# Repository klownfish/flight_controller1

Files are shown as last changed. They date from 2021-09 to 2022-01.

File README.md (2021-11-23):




The goal for the flight controller is to

1. Measure acceleration, rotation and altitude
1. Get rocket location
1. Store all measurements on-board
1. Real-time telemetry
1. Ignite explosive charges
1. Record video

So far it has been used on [rocket1](https://github.com/klownfish/rocket1) and my W.I.P guided rocket.

### Sensors

The altitude is calculated from the pressure using a BMP280 pressure sensor. The accuracy is about +-1m which is good enough for determining the apogee but acceleration and velocity is pretty much completely lost in the noise. Acceleration and rotation is gathered from a MPU9250 which sucks hard unfortunately. The gyroscope drifts rapidly and so there is no way to get the an accurate attitude estimate. Both of these sensors are available on a GY-91 breakout board.

A Ublox M8 GPS from Team Blacksheep measured the location. The Ublox chip is easy to configure and use but the module I chose does not have any moutning holes…

### Telemetry
All data is stored on a Winond NOR flash IC and it does what it’s supposed to do. I wanted to use a RF96 LoRa modem but I mixed up the numbers ordered a RF69 generic GFSK modem. It works alright so it didn’t really matter in the end. I have not conducted a real range test but the “GFSK_Rb38_4Fd76_8” profile worked for my 30m launches.

### Pyro channels
The pyro channels consist of half H-bridges connected to GND and 12V. A half bridge is necessary to keep the channel shorted when not in use. A TVS diode is connected in parallel as well to protect from electrostatic discarges. BTN7030-1EPA is an awesome “smart” half bridge IC and powers all the channels. It has built in short circuit and overheat protection. It can source 14 Amps of currents which is on the low side for what I want to do. Running of a 3s LiPo battery at 12.6v it can power a 1.1 Ohm load which is very close to the resistance of an ignitor. From empirical data it has worked four out four times so far.

As an additional safety measure a jumper can overwrite the logic output from the micro controller and force all enable pins low. Two LEDs also show if the channels are armed or not.

### Video
A runcam split 4 recorded the onboard footage and I can not recommend it. The auto record function just straight up does not work so it doesn’t record on start up. As a result you have to push a button to start the recording manually and good luck doing that when it’s mounted inside a nose cone. Good thing the camera only cost 80€ and was destroyed in a crash. I hate that camera so fucking much I am so mad AAAAAAHHH

### Guidance
This flight controller is currently the base for a guided rocket that i am developing. It's possible to connect a BMI088 IMU to the expansion port which is much more accurate than the MPU9250. The UART pins for the GPS can also be used to control 2 servos. The servos are connected to a pyro channel with an external voltage regulator.

### Dashboard
The dashboard is written in python using TK and Matplotlib.

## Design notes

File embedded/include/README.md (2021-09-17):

If you are an radio amateur please create a file named `callsign.h` that contains your callsign.

It should look like this `#define CALLSIGN "xxxxxx"`

The code will adjust the TX properties depending on if you have a license or not. 

It might be illegal to run this without an license even though the TX power is lowered since the duty cycle can go over 10%.

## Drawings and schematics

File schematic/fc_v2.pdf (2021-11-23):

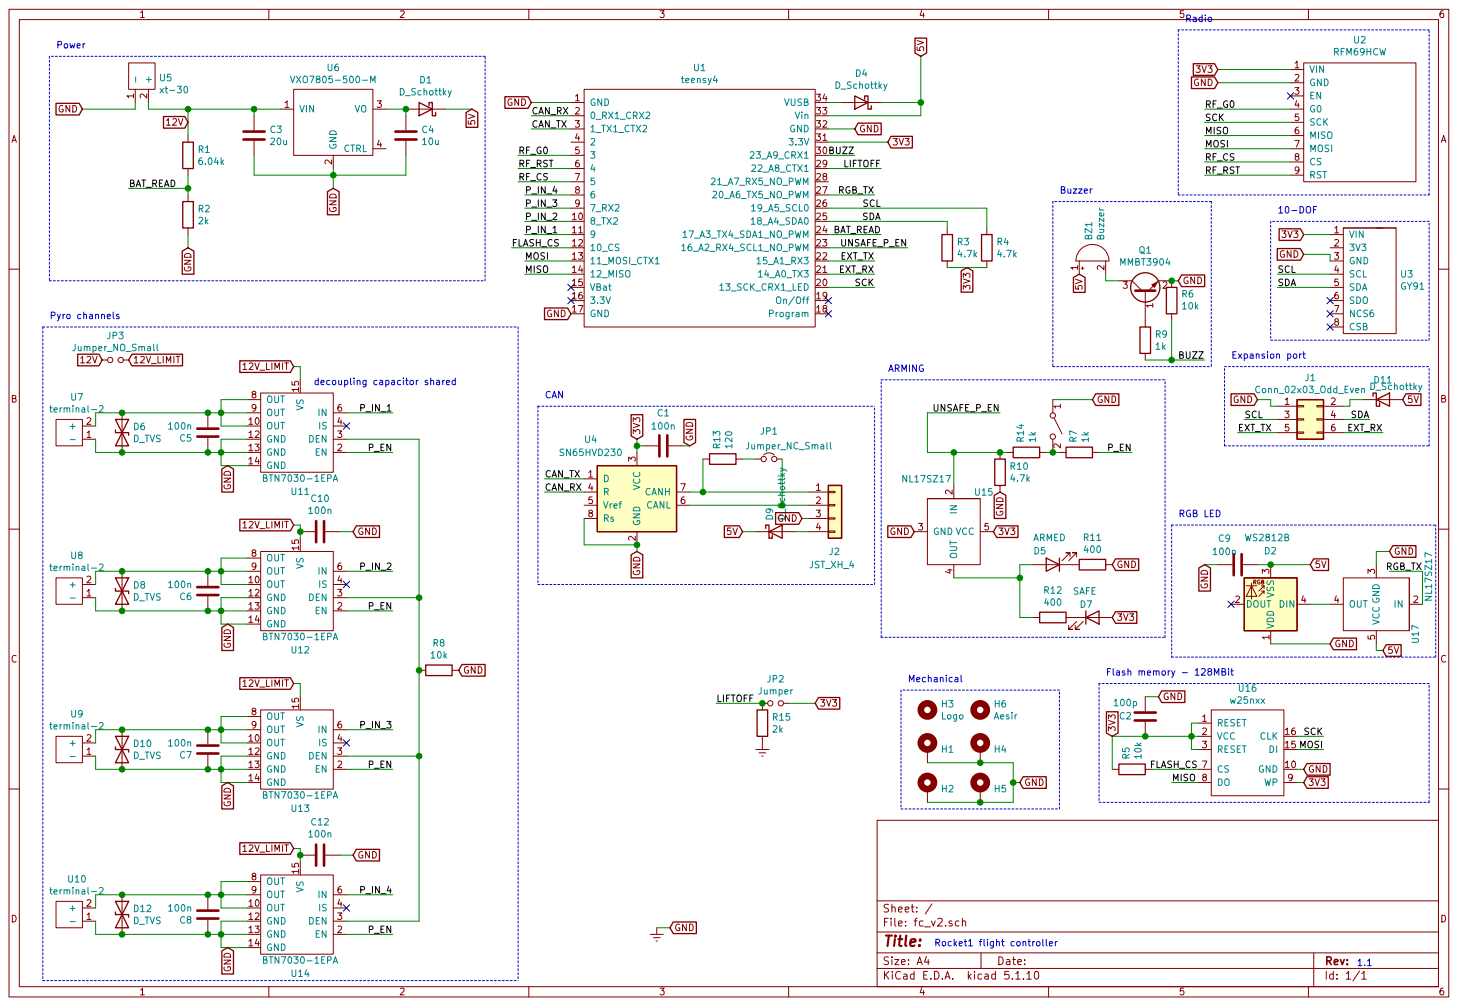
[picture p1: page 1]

Expansion port Buzzer CAN

Flash memory - 128MBit RGB LED

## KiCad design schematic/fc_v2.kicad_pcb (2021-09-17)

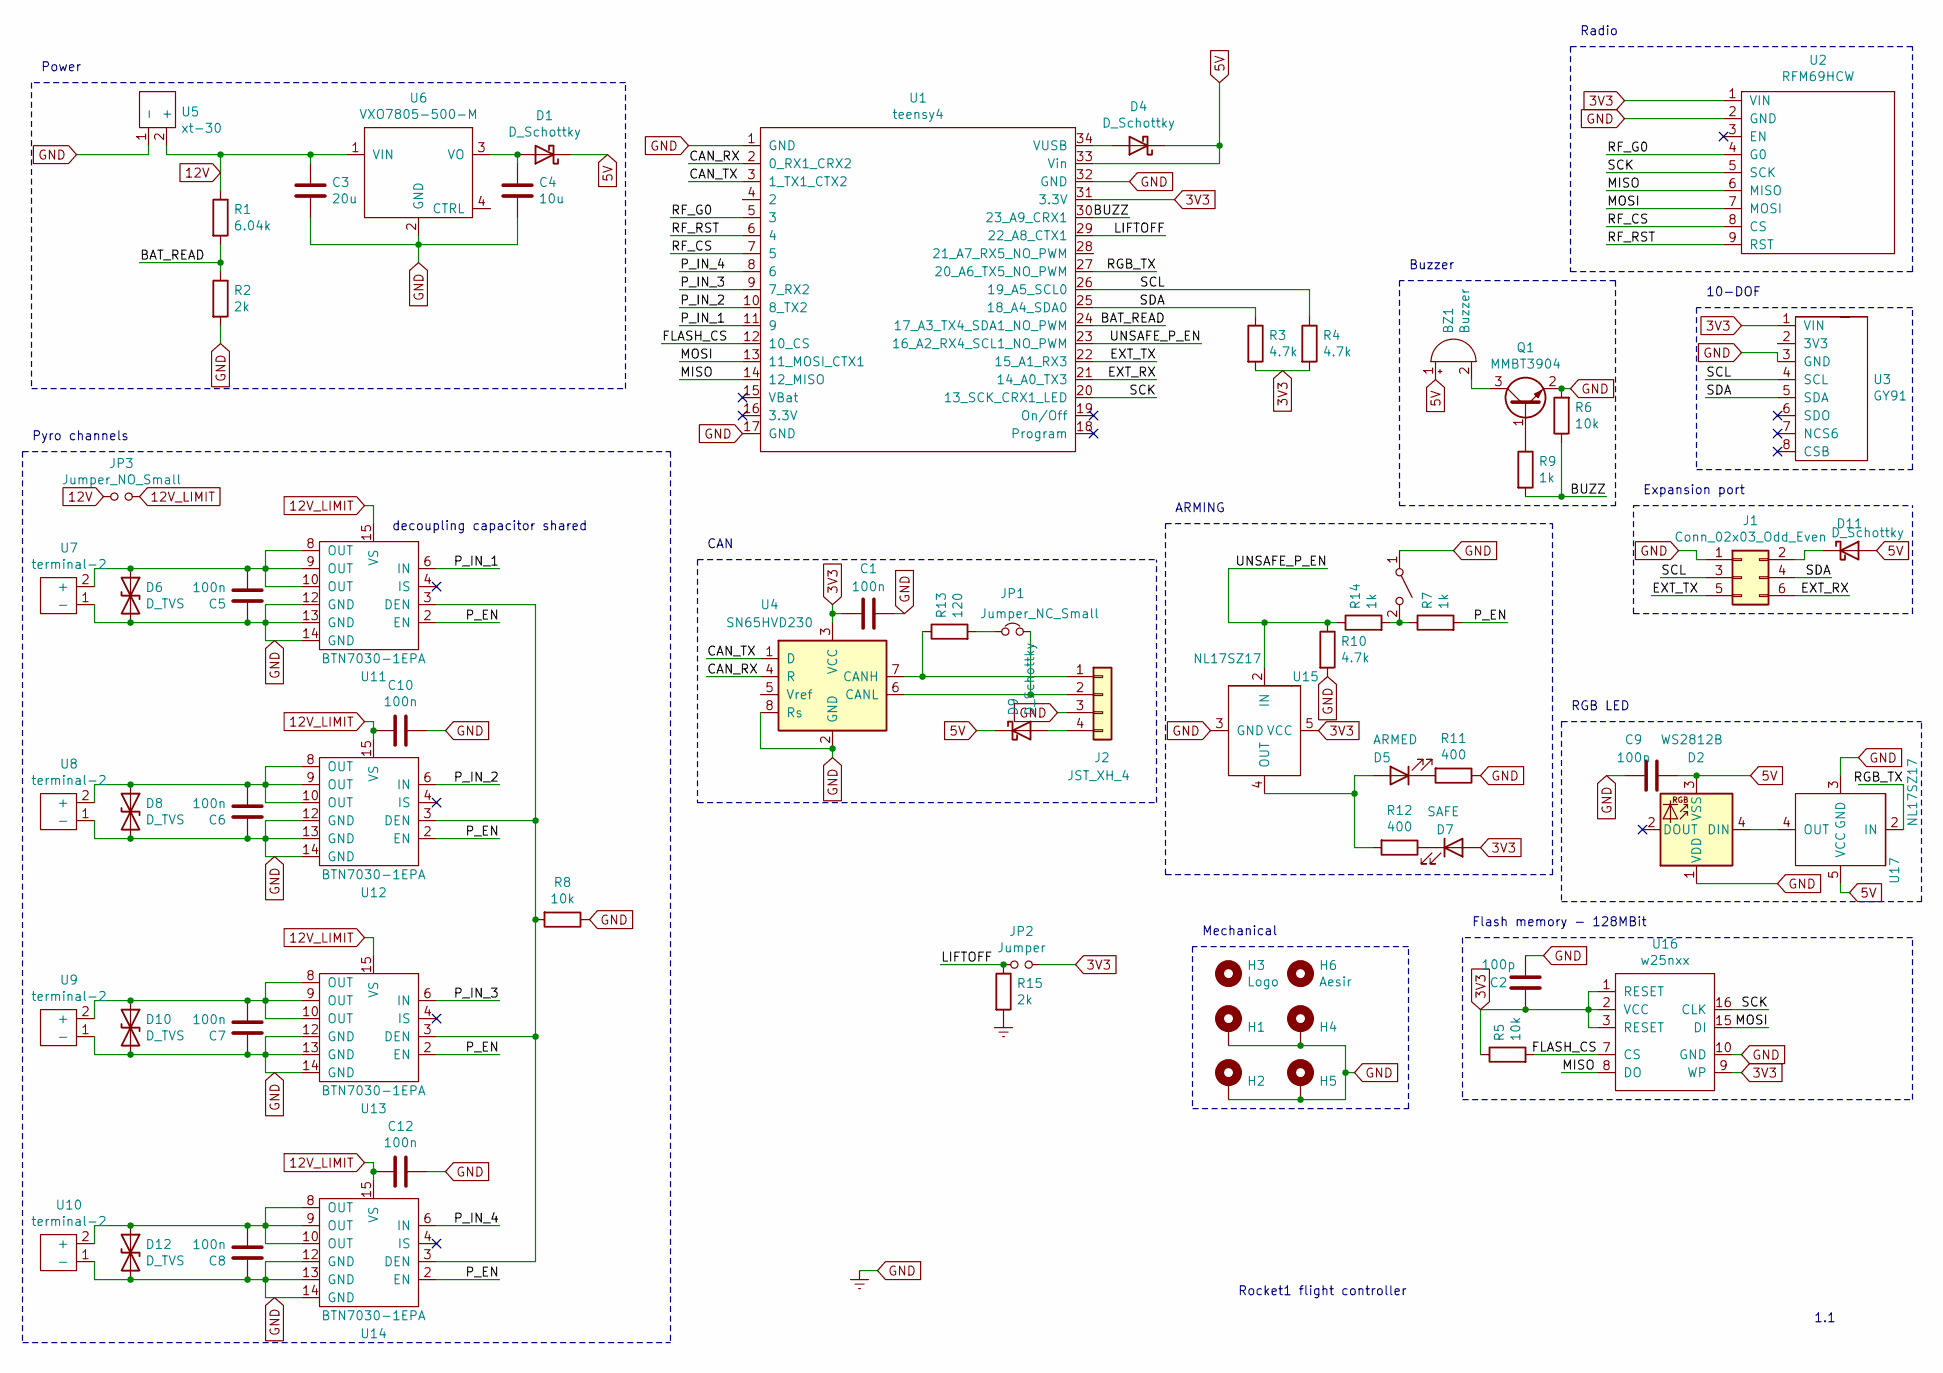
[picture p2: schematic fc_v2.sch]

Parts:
BZ1: Buzzer; CX-0905C
C1, C5, C6, C7, C8, C9, C10, C12: 100n; C_0805_2012Metric_Pad1.18x1.45mm_HandSolder
C2: 100p; C_0805_2012Metric_Pad1.18x1.45mm_HandSolder
C3: 20u; C_0805_2012Metric_Pad1.18x1.45mm_HandSolder
C4: 10u; C_0805_2012Metric_Pad1.18x1.45mm_HandSolder
D1, D4, D9, D11: D_Schottky; D_SOD-323_HandSoldering
D2: WS2812B; ws2812-through-hole-5mm
D5: ARMED; LED_0805_2012Metric_Pad1.15x1.40mm_HandSolder
D6, D8, D10, D12: D_TVS; D_0805_2012Metric_Pad1.15x1.40mm_HandSolder
D7: SAFE; LED_0805_2012Metric_Pad1.15x1.40mm_HandSolder
H1, H2, H4, H5: MountingHole_Pad; MountingHole_2.2mm_M2_Pad_Via
H3: Logo; avatar
H6: Aesir; aesir
J1: Conn_02x03_Odd_Even; PinHeader_2x03_P2.54mm_Vertical
J2: JST_XH_4; JST_XH_B4B-XH-A_1x04_P2.50mm_Vertical
JP1: Jumper_NC_Small; PinHeader_1x02_P2.54mm_Vertical
JP2: Jumper; JST_XH_B2B-XH-A_1x02_P2.50mm_Vertical
JP3: Jumper_NO_Small; R_1812_4532Metric_Pad1.30x3.40mm_HandSolder_no_silk
Q1: MMBT3904; SOT-23
R1: 6.04k; R_0805_2012Metric_Pad1.20x1.40mm_HandSolder
R2, R15: 2k; R_0805_2012Metric_Pad1.20x1.40mm_HandSolder
R3, R4, R10: 4.7k; R_0805_2012Metric_Pad1.20x1.40mm_HandSolder
R5, R6, R8: 10k; R_0805_2012Metric_Pad1.20x1.40mm_HandSolder
R7, R9, R14: 1k; R_0805_2012Metric_Pad1.20x1.40mm_HandSolder
R11, R12: 400; R_0805_2012Metric_Pad1.20x1.40mm_HandSolder
R13: 120; R_0805_2012Metric_Pad1.20x1.40mm_HandSolder
SW1: SW_DPST_x2; PinHeader_1x02_P2.54mm_Vertical
U1: teensy4
U2: RFM69HCW; Adafruit-RFM69
U3: GY91
U4: SN65HVD230; SOIC-8_3.9x4.9mm_P1.27mm
U5: xt-30; AMASS_XT30U-M_1x02_P5.0mm_Vertical
U6: VXO7805-500-M
U7, U8, U9, U10: terminal-2; terminal-small
U11, U12, U13, U14: BTN7030-1EPA; Infineon_PG-TSDSO-14-22-bottom
U15, U17: NL17SZ17; SC-74-a
U16: w25nxx; SOIC-16W_7.5x10.3mm_P1.27mm

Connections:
3V3: C1.2, C2.1, D7.2 (A), JP2.2, R3.2, R4.2, R5.1, U1.31 (3.3V), U2.1 (VIN), U3.1 (VIN), U4.3 (VCC), U15.5 (VCC), U16.1 (RESET), U16.2 (VCC), U16.3 (RESET), U16.9 (WP)
5V: BZ1.1 (-), C9.1, D1.1 (K), D2.3 (VSS), D4.1 (K), D9.1 (K), D11.2 (A), U1.33 (Vin), U17.5 (VCC)
12V: C3.1, JP3.1, R1.1, U5.2 (+), U6.1 (VIN)
12V_LIMIT: C10.2, C12.2, JP3.2, U11.15 (VS), U12.15 (VS), U13.15 (VS), U14.15 (VS)
/BAT_READ: R1.2, R2.1, U1.24 (17_A3_TX4_SDA1_NO_PWM)
/BUZZ: R6.1, R9.2, U1.30 (23_A9_CRX1)
/CAN_RX: U1.2 (0_RX1_CRX2), U4.4 (R)
/CAN_TX: U1.3 (1_TX1_CTX2), U4.1 (D)
/EXT_RX: J1.6, U1.21 (14_A0_TX3)
/EXT_TX: J1.5, U1.22 (15_A1_RX3)
/FLASH_CS: R5.2, U1.12 (10_CS), U16.7 (CS)
/LIFTOFF: JP2.1, R15.1, U1.29 (22_A8_CTX1)
/MISO: U1.14 (12_MISO), U2.6 (MISO), U16.8 (DO)
/MOSI: U1.13 (11_MOSI_CTX1), U2.7 (MOSI), U16.15 (DI)
/P_EN: R7.2, U11.2 (EN), U12.2 (EN), U13.2 (EN), U14.2 (EN)
/P_IN_1: U1.11 (9), U11.6 (IN)
/P_IN_2: U1.10 (8_TX2), U12.6 (IN)
/P_IN_3: U1.9 (7_RX2), U13.6 (IN)
/P_IN_4: U1.8 (6), U14.6 (IN)
/RF_CS: U1.7 (5), U2.8 (CS)
/RF_G0: U1.5 (3), U2.4 (G0)
/RF_RST: U1.6 (4), U2.9 (RST)
/RGB_TX: U1.27 (20_A6_TX5_NO_PWM), U17.2 (IN)
/SCK: U1.20 (13_SCK_CRX1_LED), U2.5 (SCK), U16.16 (CLK)
/SCL: J1.3, R4.1, U1.26 (19_A5_SCL0), U3.4 (SCL)
/SDA: J1.4, R3.1, U1.25 (18_A4_SDA0), U3.5 (SDA)
/UNSAFE_P_EN: R10.1, R14.1, U1.23 (16_A2_RX4_SCL1_NO_PWM), U15.2 (IN)
GND: C1.1, C2.2, C3.2, C4.2, C5.1, C6.1, C7.1, C8.1, C9.2, C10.1, C12.1, D2.1 (VDD), D6.2 (A2), D8.2 (A2), D10.2 (A2), D12.2 (A2), H1.1, H2.1, H4.1, H5.1, J1.1, J2.3, Q1.2 (E), R2.2, R6.2, R8.1, R10.2, R11.1, R15.2, SW1.1 (A), U1.1 (GND), U1.17 (GND), U1.32 (GND), U2.2 (GND), U3.3 (GND), U4.2 (GND), U4.8 (Rs), U5.1 (-), U6.2 (GND), U7.1 (-), U8.1 (-), U9.1 (-), U10.1 (-), U11.12 (GND), U11.13 (GND), U11.14 (GND), U12.12 (GND), U12.13 (GND), U12.14 (GND), U13.12 (GND), U13.13 (GND), U13.14 (GND), U14.12 (GND), U14.13 (GND), U14.14 (GND), U15.3 (GND), U16.10 (GND), U17.3 (GND)
unnamed: BZ1.2 (+), Q1.3 (C)
unnamed: C4.1, D1.2 (A), U6.3 (VO)
unnamed: C5.2, D6.1 (A1), U7.2 (+), U11.8 (OUT), U11.9 (OUT), U11.10 (OUT)
unnamed: C6.2, D8.1 (A1), U8.2 (+), U12.8 (OUT), U12.9 (OUT), U12.10 (OUT)
unnamed: C7.2, D10.1 (A1), U9.2 (+), U13.8 (OUT), U13.9 (OUT), U13.10 (OUT)
unnamed: C8.2, D12.1 (A1), U10.2 (+), U14.8 (OUT), U14.9 (OUT), U14.10 (OUT)
unnamed: D2.4 (DIN), U17.4 (OUT)
unnamed: D4.2 (A), U1.34 (VUSB)
unnamed: D5.1 (K), R11.2
unnamed: D5.2 (A), R12.2, U15.4 (OUT)
unnamed: D7.1 (K), R12.1
unnamed: D9.2 (A), J2.4
unnamed: D11.1 (K), J1.2
unnamed: J2.1, R13.1, U4.7 (CANH)
unnamed: J2.2, JP1.2, U4.6 (CANL)
unnamed: JP1.1, R13.2
unnamed: Q1.1 (B), R9.1
unnamed: R8.2, U11.3 (DEN), U12.3 (DEN), U13.3 (DEN), U14.3 (DEN)
unnamed: R7.1, R14.2, SW1.2 (B)

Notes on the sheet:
Rocket1 flight controller
1.1
Flash memory - 128MBit
Radio
Power
RGB LED
Expansion port
Buzzer
ARMING
Pyro channels
decoupling capacitor shared
Mechanical
10-DOF
CAN

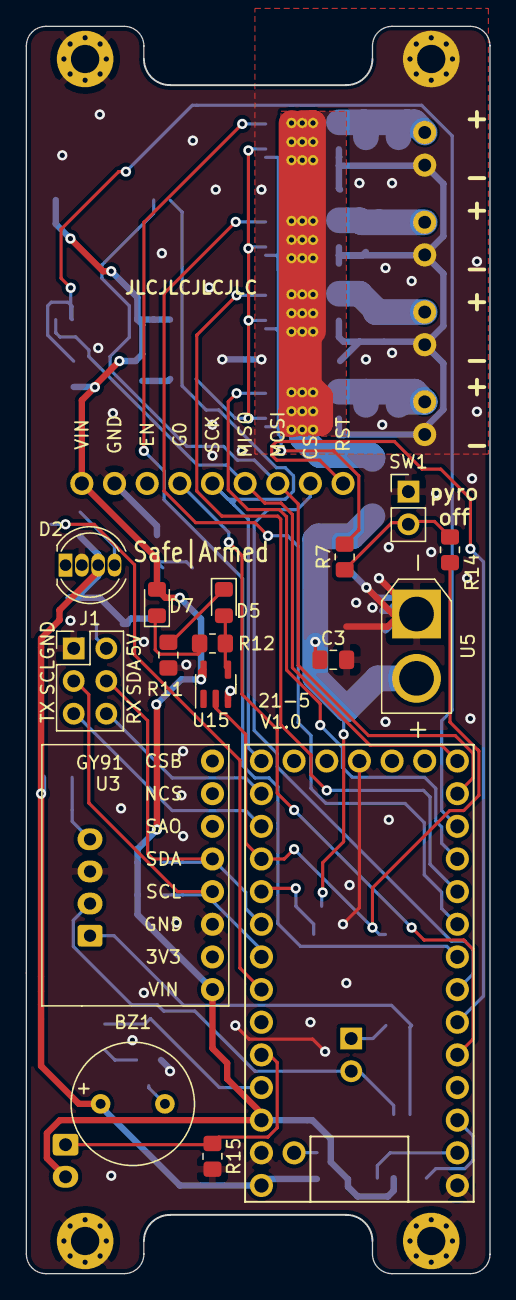
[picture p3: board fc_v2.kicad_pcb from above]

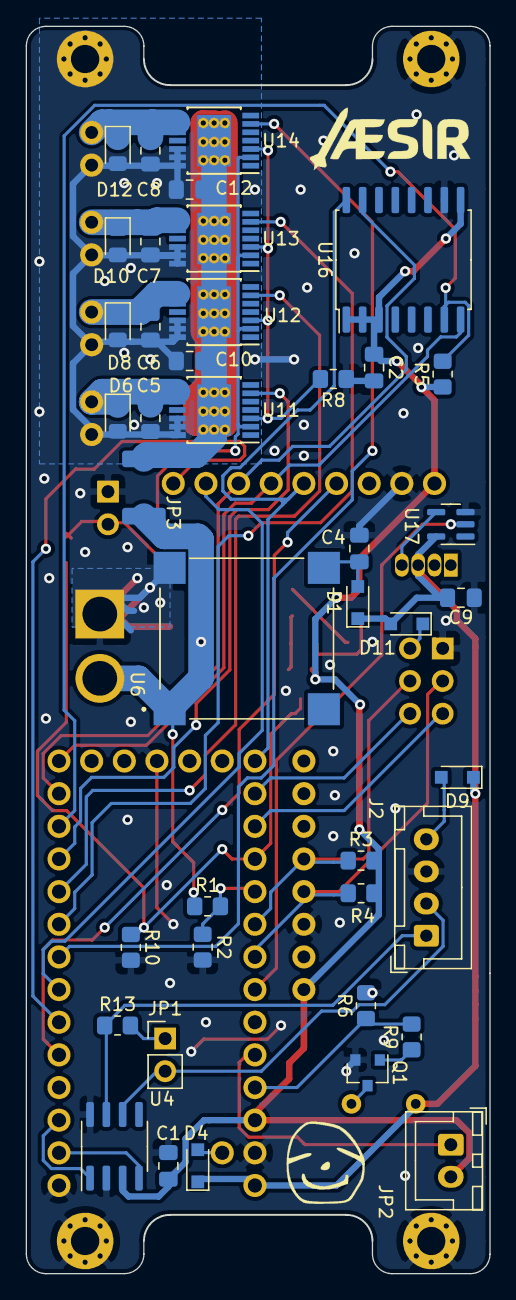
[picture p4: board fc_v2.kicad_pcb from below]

Board: 2 copper layers, 36.1 x 97.0 mm, 68 parts (47 on the bottom side), 47 nets.

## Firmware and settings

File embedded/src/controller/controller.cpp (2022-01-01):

#include <Arduino.h>
#include <SPI.h>
#include <RH_RF69.h>
#include <Adafruit_BMP280.h>
#include <elapsedMillis.h>
#include <WS2812Serial.h>
#include <Adafruit_NeoPixel.h>

#include "definitions.h" // pin and protocol definitions
#include "controller.h"
#include "rocket.h"
#include "protocol.h"
#include "Sampler.h"

//haha lolz
void dance();

#define SERIAL_DEBUG

#define TIME_HZ 1000
#define BMI_GYRO_HZ 1000
#define BMI_ACCEL_HZ 250
#define BMP_HZ 50
#define BATTERY_HZ 10
#define BATTERY_HZ 10
#define GPS_HZ 10
#define TELEMETRY_HZ 15
#define STATE_HZ 100
#define TVC_ANGLE_HZ 400

#define FLASH_TEST_BYTES 10

#define GPS_BAUD 9600

#define SERVO_MIN_PULSE 750
#define SERVO_MAX_PULSE 2250
#define SERVO_ACTUATION (55 * DEG_TO_RAD)

//#define USE_GPS
#define USE_SERVO

#ifdef USE_GPS
#ifdef USE_SERVO
#error "Both servo and gps in use"
#endif
#endif

#define KP 0.5 
#define KI 0.05
#define KD 0.2

Threads::Mutex i2c_mtx;
Threads::Mutex spi_mtx;
Threads::Mutex usb_mtx;

byte drawingMemory[3];         //  3 bytes per LED
DMAMEM byte displayMemory[12]; // 12 bytes per LED
WS2812Serial rgb(1, displayMemory, drawingMemory, PIN_RGB_TX, WS2812_RGB);
Bmi088Accel bmiAcc {Master, 0x19};
Bmi088Gyro bmiGyro {Master, 0x69};
RH_RF69 radio {PIN_RF_CS, PIN_RF_G0}; 
AsyncFlash flash {&SPI, PIN_FLASH_CS, 10000000};
MPU9250 mpu;
BMP280 bmp {Master};
GPS gps;
Servo x_servo;
Servo y_servo;
Pid x_gimbal_pid {KP, KI, KD};
Pid y_gimbal_pid {KP, KI, KD}; //output is rad*s^-2
float x_gimbal_angle = 0;
float y_gimbal_angle = 0;
Estimator estimator;
Sampler sampler;
uint32_t flash_addr = 0;
bool error = false;
bool flash_enabled = false;
bool telemetry_enabled = true;
rocket::state rocket_state = rocket::state::ready;

void threadEnd(float frequency) {
    static uint32_t start_time = micros(); 
    uint32_t end_time = micros();
    uint32_t delay = 1.0 / frequency * 1000000;
    uint32_t time_taken = end_time - start_time;

    #ifdef SERIAL_DEBUG
        if (time_taken > delay) {
            Serial.println("a thread is impossibly slow");
        }
    #endif

    threads.delay_us(delay - time_taken);
    start_time = micros();
    #ifdef SERIAL_DEBUG
        if (start_time - end_time > delay * 2) {
            Serial.println("took too long for a thread to start");
        }
    #endif
}

void enterState(rocket::state state) {
    rocket_state = state;

    switch(rocket_state) {
        case rocket::state::debug:
            break;

        case rocket::state::sleeping:
            telemetry_enabled = false;
            flash_enabled = false;
            break;

        case rocket::state::ready:
            telemetry_enabled = true;
            //estimator.set_moving();
            estimator.set_stationary(0, 90 * DEG_TO_RAD, 0);
            break;

        case rocket::state::powered_flight:
            break;

        case rocket::state::passive_flight:
            break;

        case rocket::state::falling:
            break;

        case rocket::state::landed:
            break;
    }
}

void initPins() {
    pinMode(PIN_RF_CS, OUTPUT);
    pinMode(PIN_BAT_READ, INPUT);
    pinMode(PIN_RF_RST, OUTPUT);
    pinMode(PIN_FLASH_CS, OUTPUT);
    pinMode(PIN_BUZZER, OUTPUT);
    pinMode(PIN_PYRO_ARM, OUTPUT);
    pinMode(PIN_PYRO_1, OUTPUT);
    pinMode(PIN_PYRO_2, OUTPUT);
    pinMode(PIN_PYRO_3, OUTPUT);
    pinMode(PIN_PYRO_4, OUTPUT);
    
    SPI.setMISO(PIN_MISO);
    SPI.setMOSI(PIN_MOSI);
    SPI.setSCK(PIN_SCK);
    SPI.begin();
    Wire.begin();
    Wire.setClock(400000);
    analogReadResolution(12);

    analogWriteFrequency(PIN_BUZZER, BUZZER_HZ);
    digitalWrite(PIN_RF_CS, HIGH);
    digitalWrite(PIN_PYRO_4, HIGH);
    digitalWrite(PIN_FLASH_CS, HIGH);
    digitalWrite(PIN_PYRO_ARM, LOW);
    delay(100);
}

void initServos() {
    x_servo.attach(PIN_EXT_RX, 750, 2250);
    y_servo.attach(PIN_EXT_TX, 750, 2250);
}

void initGps() {
    Serial3.begin(GPS_BAUD);
}

void restoreFlashAddr() {
    uint8_t empty_in_row = 0;
    uint8_t byte = 0;
    while (true) {
        flash.read(flash_addr, &byte, 1);
        if (byte == 0xff) {
            empty_in_row += 1;
        } else {
            empty_in_row = 0;
        }
        if (empty_in_row == FLASH_TEST_BYTES) {
            flash_addr -= FLASH_TEST_BYTES - 1;
            break;
        }
        flash_addr++;
    }
    Serial.print("restoring flash to: ");
    Serial.println(flash_addr);
}

void initFlash() {   
    if (!flash.begin(0xEF6018)) {
        Serial.println("Could not init flash chip");
        error = true;
        return;
    }
    uint8_t byte = 1;
    flash.write(0, &byte, 1);
    restoreFlashAddr();
}

void initRadio() {
    digitalWrite(PIN_RF_RST, LOW);
    delay(100);
    digitalWrite(PIN_RF_RST, HIGH);
    delay(100);
    digitalWrite(PIN_RF_RST, LOW);
    delay(100);
    if (!radio.init()) {
        Serial.println("could not initialize radio modem");
        error = true;
        return;
    }
    radio.setFrequency(RADIO_FREQUENCY);
    radio.setTxPower(TX_POWER, true);
    radio.setModemConfig(MODULATION);
    //attachInterrupt(PIN_RF_G0, rfm_interrupt, RISING);
    if (IS_HAM) { 
        radio.send(CALLSIGN, sizeof(CALLSIGN));
    }
}

void initMpu() {
    MPU9250Setting settings;
    settings.fifo_sample_rate = FIFO_SAMPLE_RATE::SMPL_125HZ;
    settings.gyro_fs_sel = GYRO_FS_SEL::G250DPS;
    settings.gyro_dlpf_cfg = GYRO_DLPF_CFG::DLPF_10HZ;
    settings.accel_fs_sel = ACCEL_FS_SEL::A4G;
    settings.accel_dlpf_cfg = ACCEL_DLPF_CFG::DLPF_10HZ;
    mpu.selectFilter(QuatFilterSel::NONE);
    mpu.ahrs(false);

    if (!mpu.setup(0x68, settings, Wire)) {
        Serial.println("could not initialize MPU");
        error = true;
        return;
    }
}

void initBmi() {
    uint8_t ret = 0;
    ret |= bmiAcc.begin();
    ret |= bmiGyro.begin();
    if (ret != 1) {
        Serial.println("could not ini BMI");
        error = true;
        return;
    }
    bmiAcc.setOdr(Bmi088Accel::Odr::ODR_400HZ_BW_145HZ);
    bmiGyro.setOdr(Bmi088Gyro::Odr::ODR_2000HZ_BW_230HZ);
}

void initBmp() {
    if (!bmp.begin(0x76)) {
        Serial.println("could not initialize BMP");
        error = true;
        return;
    }
}

void sampleGps() {
    for (;;) {
        rocket::gps_from_rocket_to_flash msg;
        if (gps.is_set(FLAG_FIX_STATUS)) {
            switch (gps.fix_status) {
                case 1:
                    msg.set_fix_type(rocket::fix_type::none);
                    break;
                case 2:
                    msg.set_fix_type(rocket::fix_type::fix2D);
                    break;
                case 3:
                    msg.set_fix_type(rocket::fix_type::fix3D);
                    break;
                default:
                    msg.set_fix_type(rocket::fix_type::none);
                    break;
            }
        } else {
            msg.set_fix_type(rocket::fix_type::none);
        }

        if (gps.is_set(FLAG_PDOP)) {
            msg.set_pdop(gps.pdop);
        } else {
            msg.set_pdop(0);
        }

        if (gps.is_set(FLAG_N_SATELLITES)) {
            msg.set_n_satellites(gps.n_satellites);
        } else {
            msg.set_n_satellites(0);
        }

        if (gps.is_set(FLAG_ALTITUDE)) {
            msg.set_altitude(gps.altitude);
        } else {
            msg.set_altitude(0);
        }

        if (gps.is_set(FLAG_LONGITUDE)) {
            msg.set_longitude(gps.longitude_degrees + gps.longitude_minutes / 60);
        } else {
            msg.set_longitude(0);
        }
        if (gps.is_set(FLAG_LATITUDE)) {
            msg.set_latitude(gps.latitude_degrees + gps.latitude_minutes / 60);
        } else {
            msg.set_latitude(0);
        }
        sendMsg(&msg);
        threadEnd(GPS_HZ);
    }
}

void sampleBmiAccel() {
    for (;;) {
        rocket::bmi_accel_from_rocket_to_flash msg;
        i2c_mtx.lock();
        bmiAcc.readSensor();
        i2c_mtx.unlock();
        float ax = bmiAcc.getAccelX_mss();
        float ay = bmiAcc.getAccelY_mss();
        float az = bmiAcc.getAccelZ_mss();
        msg.set_ax(ax);
        msg.set_ay(ay);
        msg.set_az(az);
        estimator.insert_acceleration(ax, ay, az, micros());
        sendMsg(&msg);
        threadEnd(BMI_ACCEL_HZ);
    }
}

void sampleBmiGyro() {
    for (;;) {
        rocket::bmi_gyro_from_rocket_to_flash msg;
        i2c_mtx.lock();
        bmiGyro.readSensor();
        i2c_mtx.unlock();
        float gx = bmiGyro.getGyroX_rads();
        float gy = bmiGyro.getGyroY_rads();
        float gz = bmiGyro.getGyroZ_rads();
        msg.set_gx(gx);
        msg.set_gy(gy);
        msg.set_gz(gz);
        estimator.insert_gyro(gx, gy, gz, micros());
        sendMsg(&msg);
        threadEnd(BMI_GYRO_HZ);
    }
}

void sampleBmp() {
    for (;;) {
        rocket::bmp_from_rocket_to_flash msg;
        i2c_mtx.lock();
        uint32_t wait = bmp.startMeasurment();
        i2c_mtx.unlock();
        threads.delay(wait);
        i2c_mtx.lock();
        double temp, pressure;
        bmp.getTemperatureAndPressure(temp, pressure);
        i2c_mtx.unlock();
        msg.set_pressure(pressure);
        msg.set_temperature(temp);
        sendMsg(&msg);
        threadEnd(BMP_HZ);
    }
}

void sampleBatteryVoltage() {
    for (;;) {
        rocket::battery_voltage_from_rocket_to_flash battery_msg;
        float volt = (float) analogRead(PIN_BAT_READ);
        volt = volt / ((1 << 12) - 1) * 3.3 * (6.04e3 + 2e3) / (2e3);   
        battery_msg.set_voltage(volt);
        sendMsg(&battery_msg);
        threadEnd(BATTERY_HZ);
    }
}

void sampleState() {
    for (;;) {
        rocket::state_from_rocket_to_flash state_msg;
        state_msg.set_state(rocket_state);
        sendMsg(&state_msg);
        threadEnd(STATE_HZ);
    }
}

void sampleTime() {
    for (;;) {
        rocket::ms_since_boot_from_rocket_to_flash msg;
        msg.set_ms_since_boot(millis());
        sendMsg(&msg);
        threadEnd(TIME_HZ);
    }
}

void sampleTvc() {
    for (;;) {
        rocket::tvc_angle_from_rocket_to_flash msg;
        msg.set_angle_x(x_gimbal_angle);
        msg.set_angle_y(y_gimbal_angle);
        sendMsg(&msg);
        threadEnd(TVC_ANGLE_HZ);
    }
}

void sampleTelemetry() {
    for (;;) {
        rocket::telemetry_from_rocket_to_ground msg;
        msg.set_ax(estimator.get_local_acceleration().x);
        msg.set_ay(estimator.get_local_acceleration().y);
        msg.set_az(estimator.get_local_acceleration().z);
        float r,p,y;
        estimator.get_heading().get_RPY(&r, &p, &y);
        msg.set_roll(r);
        msg.set_pitch(p);
        msg.set_yaw(y);
        msg.set_altitude(estimator.get_altitude());
        msg.set_satellites(gps.n_satellites);
        msg.set_rssi(radio.lastRssi());
        msg.set_state(rocket_state);
        msg.set_voltage(analogRead(PIN_BAT_READ));
        msg.set_flash_address(flash_addr);
        msg.set_ms_since_boot(millis());
        sendMsg(&msg);
        threadEnd(TELEMETRY_HZ);
    }
}

void updateTvc() {
    static uint32_t last_update = micros();
    uint32_t current_time = micros();
    float dt = (current_time - last_update) / 1000000;
    turbomath::Quaternion heading_quat = estimator.get_heading();
    float roll, pitch, yaw;
    heading_quat.get_RPY(&roll, &pitch, & yaw);
    float x_angular_accel = x_gimbal_pid.update(roll, dt);
    float y_angular_accel = y_gimbal_pid.update(pitch, dt); //output is radians*s^-2

    float total_thrust = estimator.get_local_acceleration().z / ROCKET_MASS;
    float moment_arm = ROCKET_MOUNT - ROCKET_COM;
    float x_thrust =  x_angular_accel * ROCKET_MOI / moment_arm;
    float y_thrust = y_angular_accel * ROCKET_MOI / moment_arm;;
    
    float x_angle = asinf(x_thrust / total_thrust);
    float y_angle = asinf(y_thrust / total_thrust);

    float mount_x_angle = cosf(yaw) * x_angle - sinf(yaw) * y_angle;
    float mount_y_angle = sinf(yaw) * x_angle + cosf(yaw) * y_angle;

    float servo_x_angle = SERVO_ACTUATION / 2 + constrain(mount_x_angle, -SERVO_ACTUATION / 2, SERVO_ACTUATION / 2);
    float servo_y_angle = SERVO_ACTUATION / 2 + constrain(mount_y_angle, -SERVO_ACTUATION / 2, SERVO_ACTUATION / 2);
    
    x_servo.writeMicroseconds(SERVO_MIN_PULSE + (SERVO_MAX_PULSE - SERVO_MIN_PULSE) * servo_x_angle / SERVO_ACTUATION);
    y_servo.writeMicroseconds(SERVO_MIN_PULSE + (SERVO_MAX_PULSE - SERVO_MIN_PULSE) * servo_y_angle / SERVO_ACTUATION);
    x_gimbal_angle = mount_x_angle;
    y_gimbal_angle = mount_y_angle;
}

void initThreads() {
    threads.setMicroTimer();
    threads.addThread(sampleBmp);
    threads.addThread(sampleBatteryVoltage);
    threads.addThread(sampleTelemetry);
    threads.addThread(sampleTime);
}


EventResponder true_yield_er;
void true_yield(EventResponderRef r) {
    threads.yield();
    true_yield_er.triggerEvent();
}

void setup() {
    true_yield_er.runFromYield();
    true_yield_er.attach(true_yield);
    true_yield_er.triggerEvent();

    //setup doesn't have to be optimized, lock everything
    i2c_mtx.lock();
    spi_mtx.lock();
    usb_mtx.lock();
    Serial.begin(BAUD);
    initPins();
    enterState(rocket::state::sleeping);
    rgb.begin();
    rgb.setPixel(0, 0);
    rgb.show();
    Master.begin(400000);
    initFlash();
    initBmp();
    //initRadio();
    initThreads();
    #ifdef USE_GPS
        initGps();
        threads.addThread(sampleGps)
    #else
        initBmi();
        initServos();
        digitalWrite(PIN_PYRO_4, HIGH);
        x_gimbal_pid.set_setpoint(0);
        y_gimbal_pid.set_setpoint(0);
        threads.addThread(sampleTvc);
        threads.addThread(sampleBmiAccel);
        threads.addThread(sampleBmiGyro);
        threads.addThread(sampleTvc);
    #endif
    if (error) {
        // not good
        rgb.setPixel(0, ERROR_COLOR);
        rgb.show();
    } else {
        // the all good song
        // dance();
        rgb.setPixel(0, OK_COLOR);
        rgb.show();
    }
    i2c_mtx.unlock();
    spi_mtx.unlock();
    usb_mtx.unlock();
}

void loop() {
    handleDataStreams();
    updateTvc();
    estimator.update(micros());
    threads.yield();
}

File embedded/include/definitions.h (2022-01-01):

#if __has_include("callsign.h")
#   include "callsign.h"
#   define TX_POWER 20
#   define IS_HAM true
#else
#   define CALLSIGN ""
#   define TX_POWER 13
#   define IS_HAM false
#endif

#define RADIO_BUF_LEN 128

#define RADIO_FREQUENCY 433.800
#define MODULATION RH_RF69::ModemConfigChoice::GFSK_Rb38_4Fd76_8

#define PIN_CAN_RX 0
#define PIN_CAN_RX 1
#define PIN_RF_G0 3
#define PIN_RF_RST 4
#define PIN_RF_CS 5
#define PIN_PYRO_4 6
#define PIN_PYRO_3 7
#define PIN_PYRO_2 8
#define PIN_PYRO_1 9
#define PIN_FLASH_CS 10
#define PIN_MOSI 11
#define PIN_MISO 12
#define PIN_SCK 13
#define PIN_EXT_RX 14
#define PIN_EXT_TX 15
#define PIN_PYRO_ARM 16
#define PIN_BAT_READ 17
#define PIN_SDA 18
#define PIN_SCL 19
#define PIN_RGB_TX 20
#define PIN_LIFTOFF 22
#define PIN_BUZZER 23

#define RED    0x160000
#define GREEN  0x001600
#define BLUE   0x000016
#define YELLOW 0x101400
#define PINK   0x120009
#define ORANGE 0x100400
#define WHITE  0x101010

#define BAUD 115200

#define BUZZER_HZ 2700

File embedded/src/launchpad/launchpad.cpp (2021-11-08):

#include <Arduino.h>
#include <Adafruit_NeoPixel.h>

#include "RH_RF69.h"
#include "DataProtocol.h"
#include "definitions.h"
#include "rocket.h"

void DataProtocolCallback(uint8_t id, uint8_t* buf, uint8_t len);

DataProtocol usb_protocol {DataProtocolCallback};
DataProtocol radio_protocol {DataProtocolCallback};
RH_RF69 radio {PIN_RF_CS, PIN_RF_G0};
Adafruit_NeoPixel rgb {1, PIN_RGB_TX};

bool error = false;

void initPins() {
    pinMode(PIN_RF_CS, OUTPUT);
    pinMode(PIN_BAT_READ, INPUT);
    pinMode(PIN_RF_RST, OUTPUT);
    pinMode(PIN_FLASH_CS, OUTPUT);
    pinMode(PIN_BUZZER, OUTPUT);
    pinMode(PIN_PYRO_ARM, OUTPUT);
    pinMode(PIN_PYRO_1, OUTPUT);
    pinMode(PIN_PYRO_2, OUTPUT);
    pinMode(PIN_PYRO_3, OUTPUT);
    pinMode(PIN_PYRO_4, OUTPUT);
    
    SPI.setMISO(PIN_MISO);
    SPI.setMOSI(PIN_MOSI);
    SPI.setSCK(PIN_SCK);
    SPI.begin();

    digitalWrite(PIN_RF_CS, HIGH);
    digitalWrite(PIN_FLASH_CS, HIGH);
    digitalWrite(PIN_PYRO_ARM, LOW);
    delay(100);
}

void initRadio() {
    digitalWrite(PIN_RF_RST, LOW);
    delay(100);
    digitalWrite(PIN_RF_RST, HIGH);
    delay(100);
    digitalWrite(PIN_RF_RST, LOW);
    delay(100);
    if (!radio.init()) {
        Serial.println("could not initialize radio modem");
        error = true;
        return;
    }
    radio.setFrequency(FREQUENCY);
    radio.setTxPower(TX_POWER, true);
    radio.setModemConfig(MODULATION);
    if (IS_HAM) { 
        radio.send(CALLSIGN, sizeof(CALLSIGN));
    }
}

void DataProtocolCallback(uint8_t id, uint8_t* buf, uint8_t len) {
    rocket::parse_message(id, buf);
}

void rocket::rx(rocket::handshake_from_everyone_to_everyone msg) {
    rocket::handshake_from_everyone_to_everyone response;
    uint8_t out_buf[response.get_size() + HEADER_SIZE];
    uint8_t index = 0;
    DataProtocol::build_buf(&response, out_buf, &index);
    delay(200);
    Serial.write(out_buf, index);
    delay(500);
}

void rocket::rx(rocket::arm_pyro_from_ground_to_launchpad msg) {
    digitalWriteFast(PIN_PYRO_ARM, msg.get_armed());
}

void rocket::rx(rocket::enable_pyro_from_ground_to_launchpad msg) {
    uint8_t channel;
    switch (msg.get_channel()) {
        case 1:
            channel = PIN_PYRO_1;
            break;
        case 2:
            channel = PIN_PYRO_2;
            break;
        case 3:
            channel = PIN_PYRO_3;
            break;
        case 4:
            channel = PIN_PYRO_4;
            break;
    }
    
    tone(PIN_BUZZER, BUZZER_HZ, 300);
    delay(600);
    tone(PIN_BUZZER, BUZZER_HZ, 300);
    delay(600);
    tone(PIN_BUZZER, BUZZER_HZ, 300);
    delay(600);

    tone(PIN_BUZZER, BUZZER_HZ, 1000);
    delay(1500);
    
    digitalWriteFast(PIN_PYRO_1, HIGH);
    delay(500);
    digitalWriteFast(PIN_PYRO_1, LOW);
}

void setup() {
    Serial.begin(BAUD);
    initPins();
    rgb.begin();
    initRadio();
    if (!error) {
        rgb.setPixelColor(0, OK_COLOR);
        rgb.show();
    } else {
        rgb.setPixelColor(0, ERROR_COLOR);
        rgb.show();
    }
}

void loop() {
    uint8_t radio_buf[255];
    uint8_t radio_len = 255;
    while (Serial.available() > 0) {
        usb_protocol.parse_byte(Serial.read());
    }
    if (radio.recv(radio_buf, &radio_len)) {
        radio_protocol.parse_bytes(radio_buf, radio_len);
    }
}
